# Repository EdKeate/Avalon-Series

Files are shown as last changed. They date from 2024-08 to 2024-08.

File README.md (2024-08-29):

> [!WARNING]
> This Project is a work in progress and not yet finished. Files are uploaded and repository publicised to take onboard feedback, advice and hopefully locate eager collaborators.

> [!WARNING]
> These components are **NOT** compatible with **ANY** Future Motion™ products including, but not limited to: Onewheel, Onewheel+, Onewheel+ XR, Onewheel Pint, Onewheel Pint X, Onewheel GT, Onewheel GT S-series, Onewheel GT S-series "Rally edition".
> 
> Attempting to use **ANY** of the components inside this repository with Future Motion™ products will result in serious injury or death. Do not attempt.

<p align="Center">
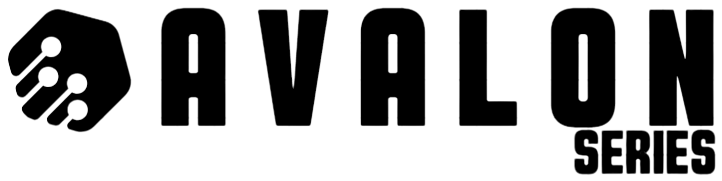
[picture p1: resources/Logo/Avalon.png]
Avalon Logo
  
</p>

---

> **Avalon:** "The isle of the dead, an island paradise where King Arthur and other heroes are taken after death"

The Avalon Project is an open-source Self-Balancing Electric-Skateboard project focused on customizability, power, and networking. All [PCB](https://resources.altium.com/p/what-is-a-pcb), [CAD](https://www.techtarget.com/whatis/definition/CAD-computer-aided-design), Code and project files can be find inside this repository.

> Distributed under the [Apache 2.0 License](https://www.apache.org/licenses/LICENSE-2.0). Read [LICENSE.md](LICENSE.md)

---

- [Odyssey](Odyssey) Flagship 134.4V 1KWh+ Performance System **(ETA: End of Q3 2024)**
- [Apollo:](Apollo) Capable 138.8V 500Wh+ Pocket Rocket **(ETA: End of Q1 2025)**
- [Fenrir:](Fenrir) Powerful 100.8V 400Wh+ Lightweight Commuter **(ETA: Start of Q4 2025)**

>See also: [InfoBar](infobar), E-ink external display for the Avalon Series

---

[](https://github.com/EdKeate/Avalon-Series?tab=readme-ov-file#odyssey)

> On the [Odyssey](https://www.britannica.com/topic/Odyssey-epic-by-Homer), Odysseus faces numerous trials, including monsters and gods, on his decade-long journey home from the Trojan War to Ithaca.

The **Odyssey** is the Flagship board in the **Avalon Series** of self-balancing boards. Boasting a voltage range of 100.8V to 134.4V, 1KWh+ of capacity, 1k+ Lumen lighting (yes actually), Movement wake detection and Fingerprint Sensing (no, seriously). No compromises were taken during the design process. 

> [!IMPORTANT]
> Please read [Odyssey Board Disclaimer](#odyssey-board-disclaimer)

### Features
- Voltage(V): 134.4V to 100.8V
- Range(Km): 50-90 (134.4V), 40-60 (100.8V)
- Speed: [Yes](https://www.youtube.com/watch?v=zXf44tSWhBQ) (Over 2000W+ compared to video)
- 10 x [70-100 Lumen White LEDs](https://www.lcsc.com/datasheet/lcsc_datasheet_2309141627_JNJ-OPTOELECTRONICS-JNJ-LTJH0111W60-26mil-8000-9000K_C7500127.pdf) (PWM Configurable)
- 22 x [SK68812RGBW](https://cdn-shop.adafruit.com/product-files/2757/p2757_SK6812RGBW_REV01.pdf) Addressable LEDs
- [Fingerprint Sensor](https://cdn.shopify.com/s/files/1/0176/3274/files/104474-datasheet.pdf?v=1650622001) with user profiles and logging
- [ESPHome](https://esphome.io/) integration

### Powertrain 
- Controller: [JetFleet F6](https://www.jetfleet.store/product/15108255/controller-jetfleet-f6), [TRONIC X12](https://tronicsystems.com/products/x12-bareboard-no-enclosure), [ENNOID-ESC MK8](https://www.ennoid.me/esc/150v-esc)
- BMS: [ENNOID-BMS Master-XLITE](https://www.ennoid.me/bms/master-xlite), [ENNOID-BMS XLITE-V4](https://www.ennoid.me/bms/xlite-v4), [Flipsky 4S-30S 20A BMS](https://flipsky.net/collections/bms/products/flipsky-4s-30s-20a-bms-protection-board-hardware-ternary-polymer-lithium-battery-only-charge-bms-board-for-onewheel-ebik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)
- Cells: [Molicel P42A](https://www.molicel.com/wp-content/uploads/INR21700P42A-V4-80092.pdf), [Molicel P45B](https://www.molicel.com/wp-content/uploads/INR21700P45B_1.2_Product-Data-Sheet-of-INR-21700-P45B-80109.pdf), [Samsung 50S](https://www.dnkpower.com/wp-content/uploads/2022/07/SAMSUNG-INR21700-50S-Cell-Specification.pdf), [EVE 40P](https://www.rcscomponents.kiev.ua/datasheets/INR21700_40P.pdf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), [Samsung 40T](https://www.dnkpower.com/wp-content/uploads/2019/02/SAMSUNG-INR21700-40T-Datasheet.pdf), [TenPower 40TG](https://www.tenpowercell.com/wp-content/uploads/2022/12/TP-INR21700-40TG-Product-Datasheet-v1.4.1.pdf), [Sony VT6A](https://www.imrbatteries.com/content/murata_us21700vtc6a.pdf)
> If you are unsure what Cell, Controller or BMS to use for this board, consider consulting an experienced VESC builder for assembly assistance. Please refer them to this repository.

### Image
<p align="Center">
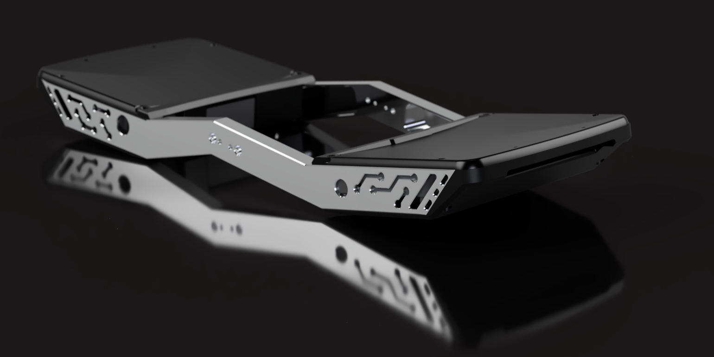
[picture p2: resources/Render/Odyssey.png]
Odyssey Frame
  
</p>

## Odyssey Parts

- [Odyssey Control Board](#odyssey-control-board)
- [Odyssey Lightsym Bars](#odyssey-lightsym-bar)
- [Odyssey Controller Box](#odyssey-controller-box)
- [Odyssey Battery Box](#odyssey-battery-box)
- [Odyssey Rails](#odyssey-rails)
- [Odyssey Footpads](#odyssey-footpads)
- [Odyssey Bumpers](#odyssey-bumpers)
- [Odyssey Fender](#odyssey-fender)
- [Odyssey Axle Blocks](#odyssey-axle-blocks)
- [Avalon Series Tools & Hardware](#avalon-series-tools--hardware)

## Odyssey Control Board

[EasyEDA Files](Odyssey/Control%20Board/PCBs/EasyEDA)

[ESP32 Code + Flashing](Odyssey/Control%20Board/Code)

The **Odyssey Control Board** is designed inside [EasyEDA](EasyEDA.com) and is intended to be assembled using [JLCPCB Economic Assembly](https://jlcpcb.com/capabilities/pcb-assembly-capabilities). 

The Control Board communicates with/powers:
- The [R503-M22 Fingerprint Sensor](https://cdn.shopify.com/s/files/1/0176/3274/files/104474-datasheet.pdf?v=1650622001) 
- 2 x [Odyssey Lightsym Bars](#odyssey-lightsym-bar)
- ESP Home integration using an [Espressif Systems ESP32-WROOM-32E-N8](https://www.lcsc.com/datasheet/lcsc_datasheet_2403071012_Espressif-Systems-ESP32-WROOM-32E-N8_C701342.pdf) as the [MCU](https://en.wikipedia.org/wiki/Microcontroller)
- VESC Power ([SSR Relay](https://www.lcsc.com/datasheet/lcsc_datasheet_1808101047_TOSHIBA-TLP172GM-TPL-E-O_C261926.pdf) control)

### Always on efficiency
The Control board is an **Always-On** Deep-Sleep system, this may cause concerns over [parasitic drain](https://www.uti.edu/blog/automotive/parasitic-battery-drain) for some users, however, the ultra-efficient design and massive battery pack allows for over ~25 years battery life while active. Below shows an example of how to calculate this for yourself:

1. [ESP32](https://www.espressif.com/sites/default/files/documentation/esp32_datasheet_en.pdf) Power consumption (Active)

$$
P_{active} = V_{out} \times I_{active}
$$

$$
P_{active} = 3.3V \times 240mA = 792mW
$$

$$
P_{in} = \frac{P_{active}}{\text{LDO Efficiency}}
$$

$$
P_{in} = \frac{792mW}{0.66} = 1.2W
$$

2. [ESP32](https://www.espressif.com/sites/default/files/documentation/esp32_datasheet_en.pdf) Power consumption (Deep-Sleep)

$$
P_{deep-sleep} = V_{out} \times I_{deep-sleep}
$$

$$
P_{deep-sleep} = 3.3V \times 10\mu A = 33\mu W
$$

$$
P_{in-deep-sleep} = \frac{P_{deep-sleep}}{0.66} = 50\mu W
$$

3. Account for [buck converter efficiency](https://www.meanwellusa.com/upload/pdf/RDDW60/RSDW60,RDDW60-spec.pdf) (Active)

$$
P_{bat} = \frac{P_{in}}{\text{Buck Efficiency}} 
$$

$$
P_{bat} = \frac{1.2W}{0.89} = 1.35W 
$$

**High Voltage**

$$
I_{in} = \frac{P_{bat}}{V_{battery}} = \frac{1.35W}{126V} \approx 10.7mA
$$

**Low Voltage**

$$
I_{in} = \frac{P_{bat}}{V_{battery}} = \frac{1.35W}{90V} \approx 15mA
$$

4. Average Current Calculation (Active)

$$
I_{active} = \frac{10.7mA + 15mA}{2} \approx 12.85mA
$$

5. Account for [buck converter efficiency](https://www.meanwellusa.com/upload/pdf/RDDW60/RSDW60,RDDW60-spec.pdf) (Deep-sleep)

$$
P_{bat-deep-sleep} = \frac{50\mu W}{0.89} = 56\mu W 
$$

**High Voltage**

$$
I_{deep-sleep} = \frac{P_{bat-deep-sleep}}{126V} \approx 0.44\mu A
$$

**Low Voltage**

$$
I_{deep-sleep} = \frac{P_{bat-deep-sleep}}{90V} \approx 0.62\mu A
$$

6. Average Current Calculation (Deep-Sleep)

$$
I_{deep-sleep-avg} = \frac{0.44\mu A + 0.62\mu A}{2} \approx 0.53\mu A
$$

7. Average Current consumption (Combined 5min intervals)

$$
I_{avg} = 12.85mA \times \frac{1}{300} + 0.53\mu A \times \frac{299}{300}
$$

$$
I_{avg} \approx 0.0428mA + 0.53\mu A \approx 0.043mA
$$

8. Battery Capacity Input

$$
\text{Battery Life} = \frac{10,000 mAh}{43\mu A} \approx 232,558 hours = 9689 days = 26.5 years
$$

> [!NOTE]
> Odyssey Control board will enter recovery mode when low voltage (2.7*Series Count). Deep-SLeep interval is upped to a locked 1 hour interval when below threshold. 

>You will also need to purchase parts from [Digikey](https://www.digikey.co.uk/en/mylists/list/NP048JOWBK). See [Electronics Purchasing Guide](#Electronics-Purchasing-Guide) for more information.

> [!CAUTION]
> The Odyssey Control Board is uses the high voltage battery DC input. Ensure proper safety measures are used to prevent damage to ~~battery~~ everything ~~within 5 mile radius~~.
#### Schematic

<p align="Left">
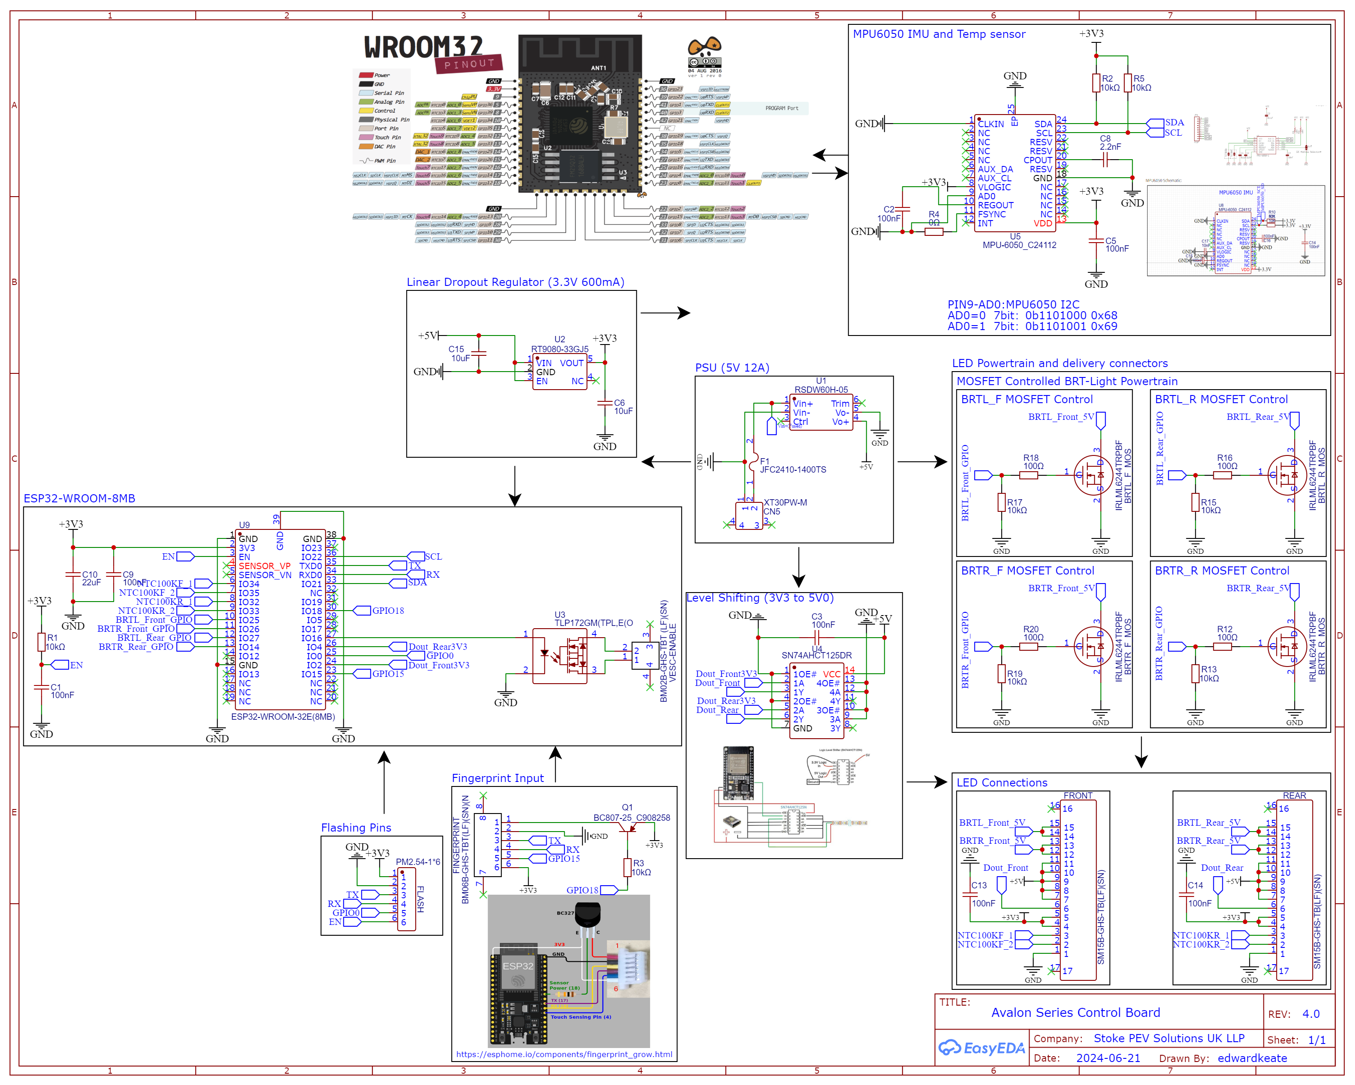
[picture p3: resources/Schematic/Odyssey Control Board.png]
Odyssey Control Board Schematic
  
</p>

#### PCB

**Top**

<p align="Left">
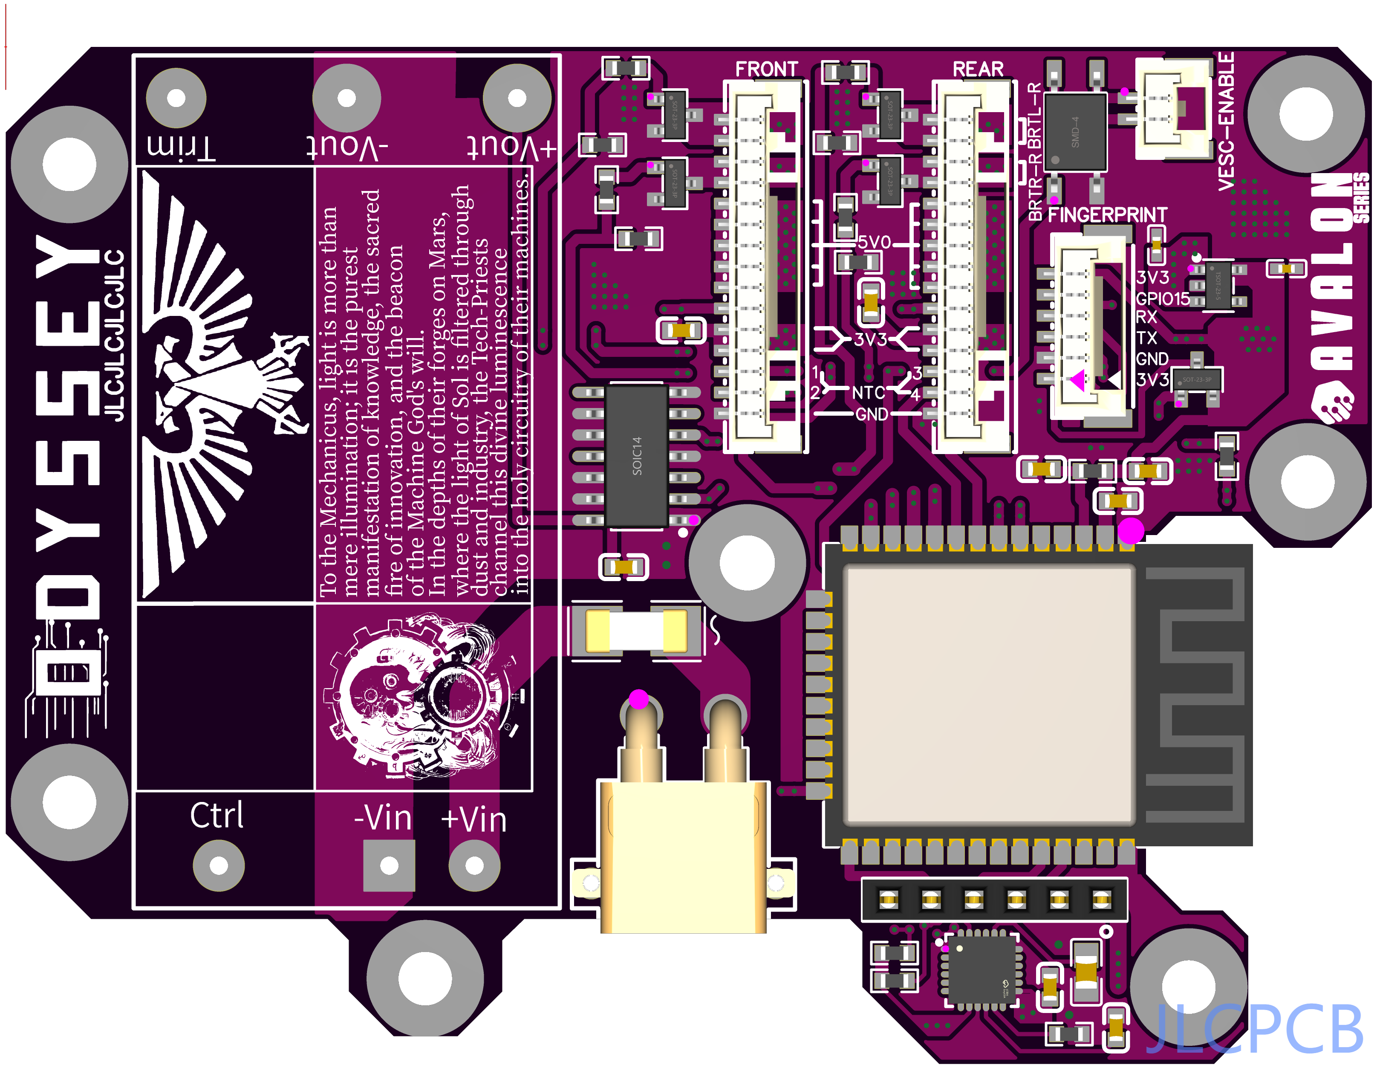
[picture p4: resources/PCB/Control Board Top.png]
Odyssey Control Board PCB (Top)
  
</p>

**Bottom**

<p align="Left">
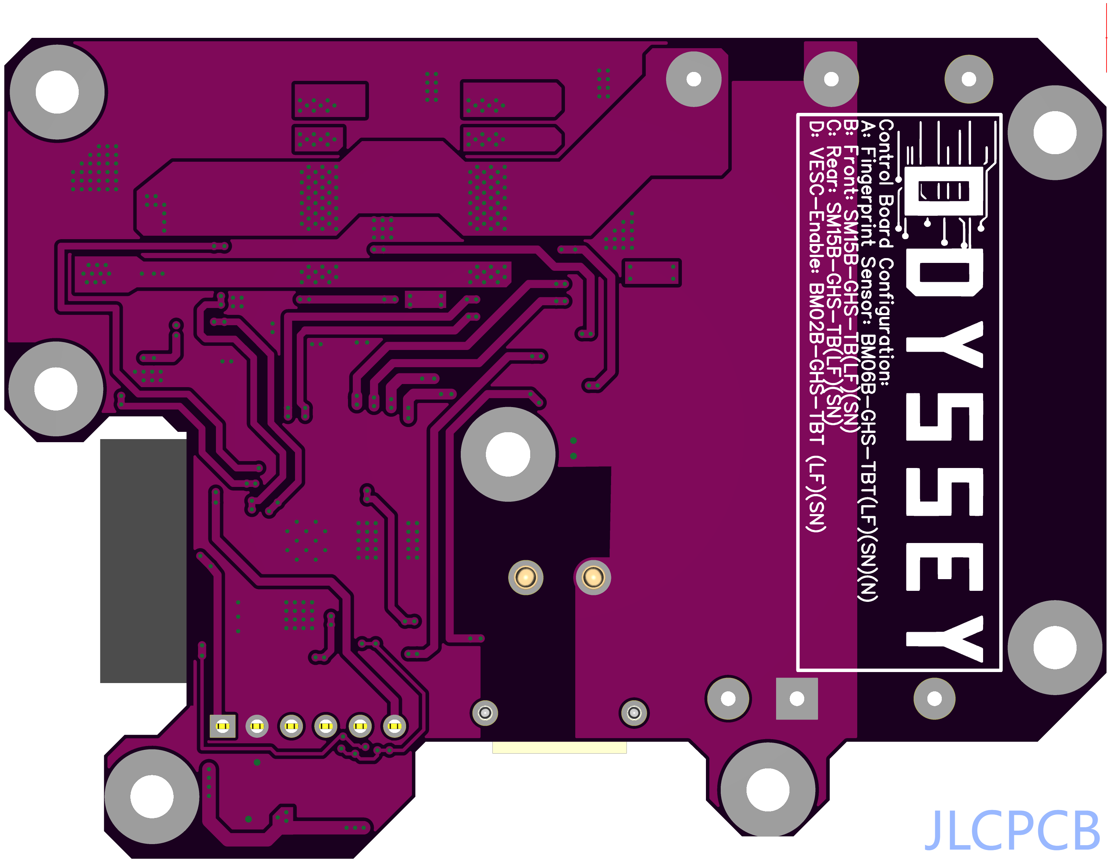
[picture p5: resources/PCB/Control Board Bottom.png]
Odyssey Control Board PCB (Bottom)
  
</p>

> [!TIP]
> Control Boards are designed for expandability. A powerful and efficient 5V rail is integrated into the Schematics, but not the PCB or BOM. See [files](Odyssey/Control%20Board/PCBs/EasyEDA) for more information.

## Odyssey LightSym Bar
[EasyEDA Files](Odyssey/LightSym%20Bar/PCBs/EasyEDA)

The **Odyssey LightSym Bar** is designed inside [EasyEDA](EasyEDA.com) and is intended to be assembled using [JLCPCB Economic Assembly](https://jlcpcb.com/capabilities/pcb-assembly-capabilities). 

The LightSym Bar has 15 inputs:
- 5 x 5V
- 2 x 3V3
- 2 x NTC100K
- 2 x BRTL
- 2 x BRTR
- 1 x Din
- 1 x GND

The labels on these inputs correlates with the labels on the [Odyssey Control Board](#odyssey-control-board).

> You will also need to purchase parts from [Digikey](https://www.digikey.co.uk/en/mylists/list/NP048JOWBK). See [Electronics Purchasing Guide](#electronics-purchasing-guide) for more information.
#### Schematic

<p align="Left">
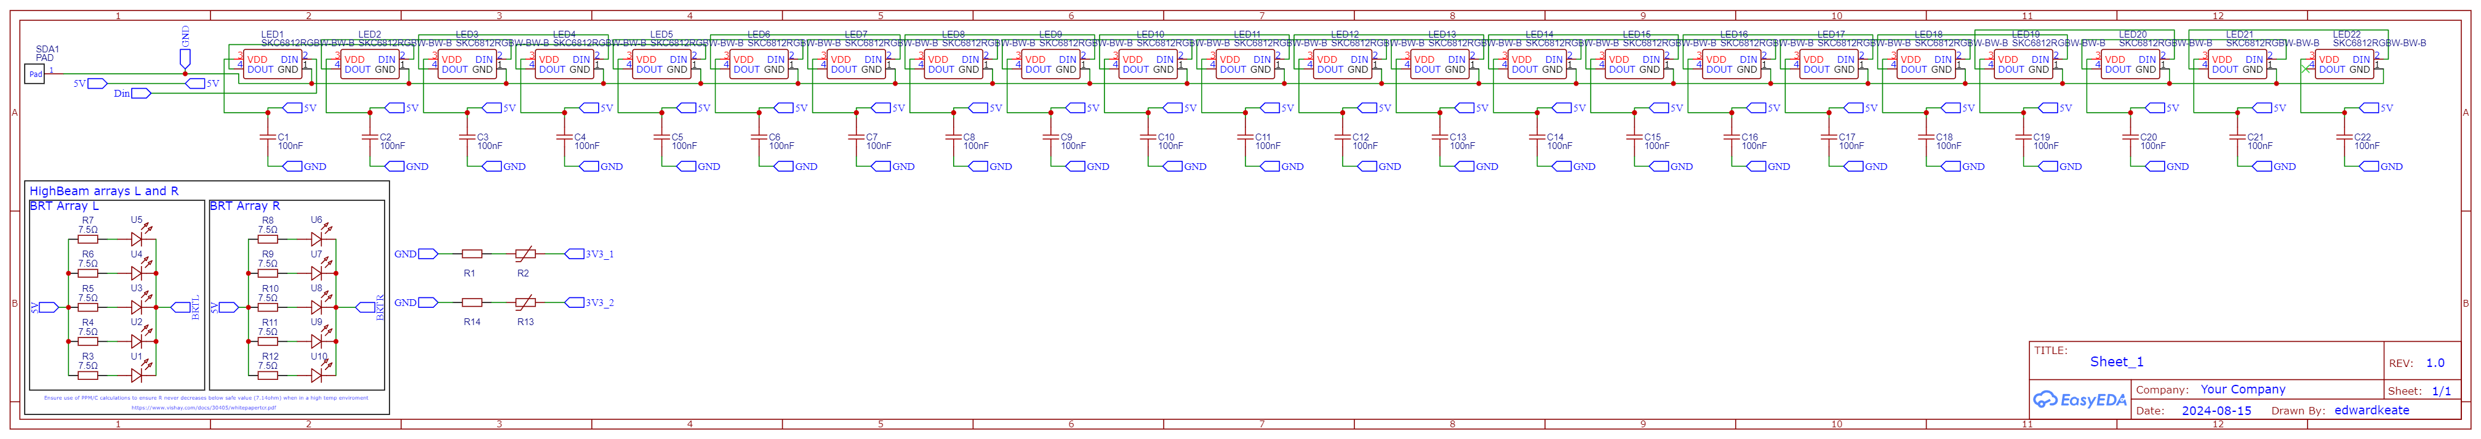
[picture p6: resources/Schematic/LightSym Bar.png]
OdysseyLightSym Bar Schematic
  
</p>

#### PCB

**Top**

<p align="Left">
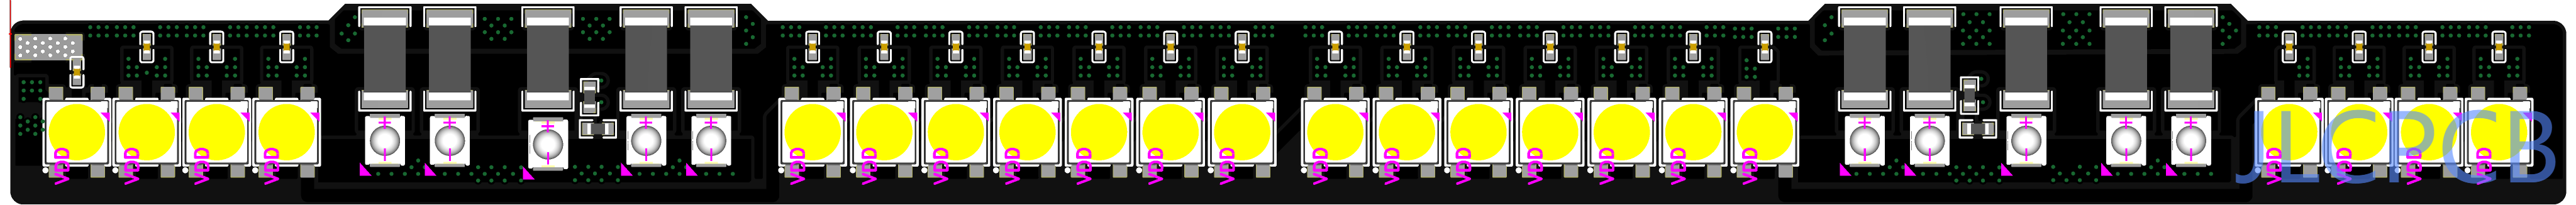
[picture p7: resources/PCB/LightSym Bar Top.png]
Odyssey LightSym Bar PCB Top
  
</p>

**Bottom**

<p align="Left">
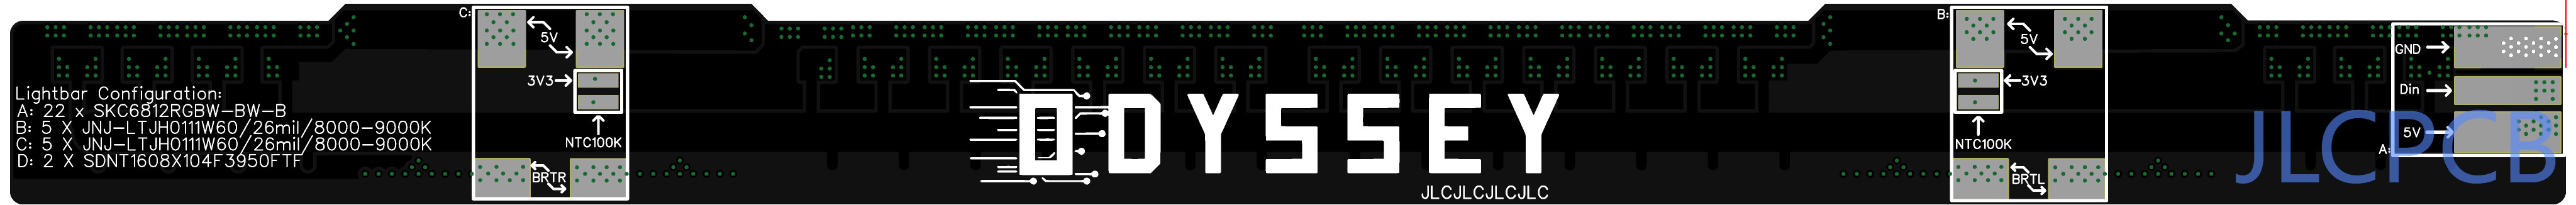
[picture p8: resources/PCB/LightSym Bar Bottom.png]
Odyssey LightSym Bar PCB Bottom
  
</p>

## Odyssey Controller Box
[CAD Files](Odyssey/Controller%20Casing)

The **Odyssey Controller Box** is a split pack enclosure designed for 6S2P 21700. For Controller & Cell options, please see the [Powertrain](#powertrain) section. 
### Features:
- **Dual** [TPU](https://formlabs.com/uk/blog/complete-guide-tpu-3d-printing/) O-ring
- [R503-M22 Fingerprint Sensor](https://cdn.shopify.com/s/files/1/0176/3274/files/104474-datasheet.pdf?v=1650622001) 
- [Superflux Connector](https://www.fungineers.us/products/superflux-female-connector)
- Dual Compartment Design
- M20 Gland Hole
- Steel reinforcement bolt system

> [!TIP]
>See the [Odyssey 3D Printing Guidelines](#odyssey-3d-printing-guidelines) for information on how to manufacture your Controller Box.
#### Image

<p align="Left">
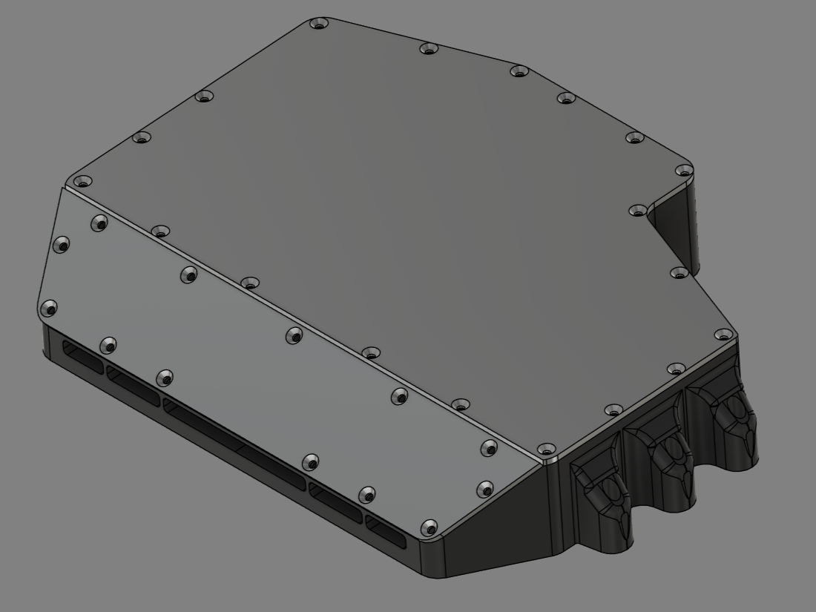
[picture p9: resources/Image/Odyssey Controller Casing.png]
Odyssey Controller Casing Image
  
</p>

#### Render

<p align="Left">
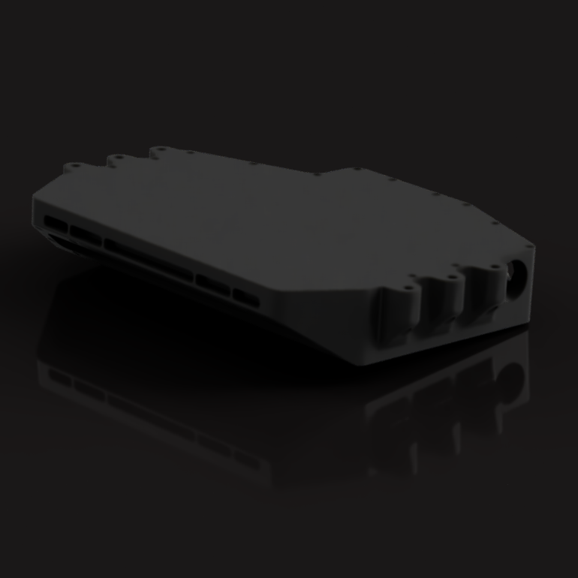
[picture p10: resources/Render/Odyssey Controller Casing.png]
Odyssey Controller Casing Render
  
</p>

## Odyssey Battery Box
[CAD Files](Odyssey/Battery%20Casing)

The **Odyssey Battery Box** has capacity for 24S2P 21700. For cell and BMS options, please see the [Powertrain](#powertrain) section. 
### Features:
- **Dual** [TPU](https://formlabs.com/uk/blog/complete-guide-tpu-3d-printing/) O-ring
- [GX16](https://www.sunrom.com/download/663.pdf) Charge port
- M20 Gland Hole
- Steel reinforcement bolt system

> [!TIP]
>See the [Odyssey 3D Printing Guidelines](#odyssey-3d-printing-guidelines) for information on how to manufacture your Battery Casing.
#### Image

<p align="Left">
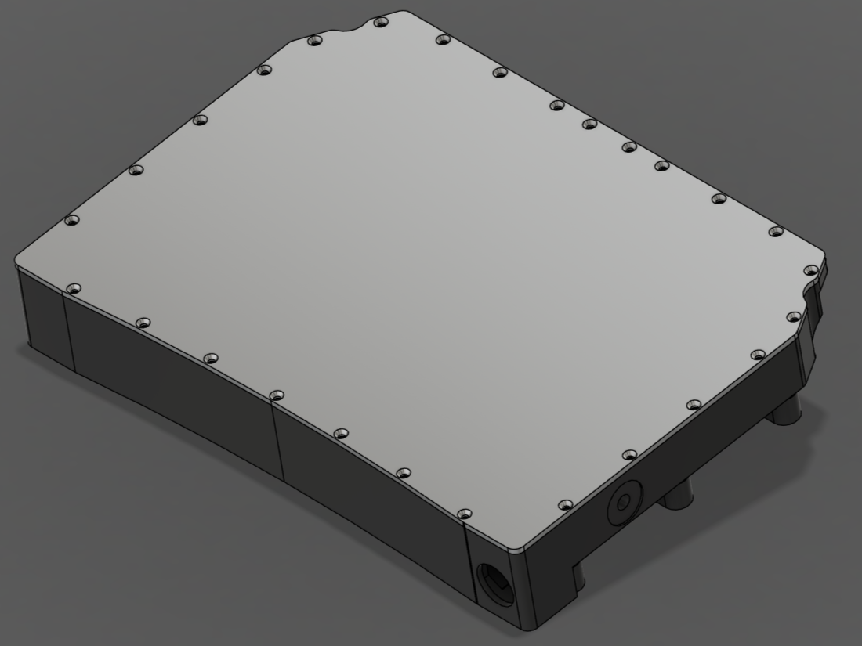
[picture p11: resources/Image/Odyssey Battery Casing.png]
Odyssey Battery Casing Image
  
</p>

#### Render

<p align="Left">
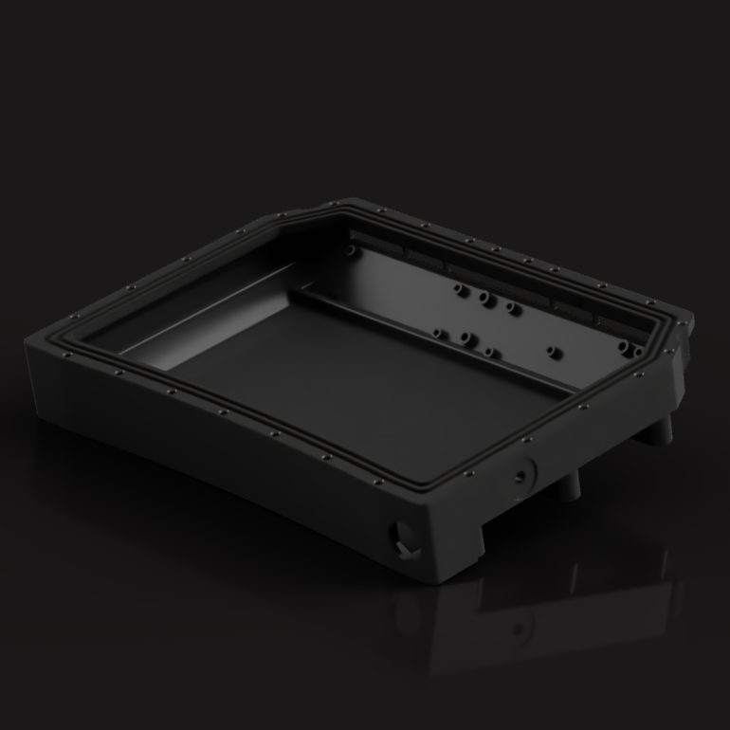
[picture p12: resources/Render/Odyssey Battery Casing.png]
Odyssey Battery Casing Render
  
</p>

## Odyssey Series Rails
[CAD Files](Odyssey/Rails)

The **Odyssey Series** has several unique rail designs. Find yours here:
- [Odyssey Rails](#Odyssey-rails)
- [Odyssey Rails (Skeletonised)](#Odyssey-rails)
### Odyssey Rails (Skeletonised)
The Flagship rails. Designed to be **lighter-weight** and strong using a completely unique skeletisation design. 
**Statistics:**
- 12" wheel-well (BTG)
- Unique "Trace" skeletisation
- 5°lowered, 3° lifted
- 4° tail lift
#### Image

**Left Rail**

<p align="Left">
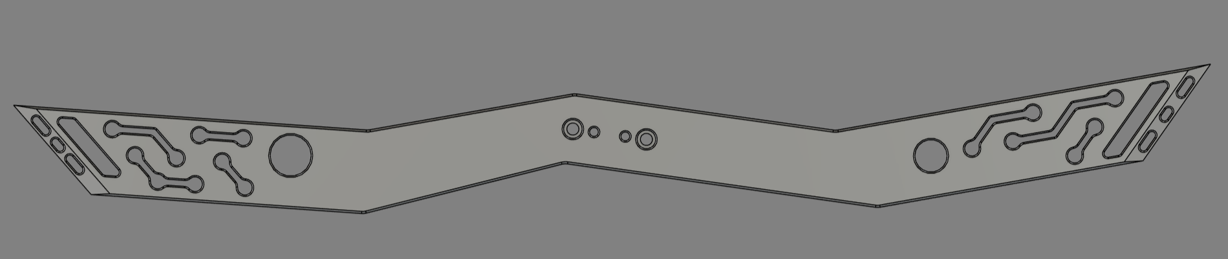
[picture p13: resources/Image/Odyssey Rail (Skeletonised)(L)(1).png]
Odyssey Rail (Skeletonised)(L)(1)
  
</p>

<p align="Left">
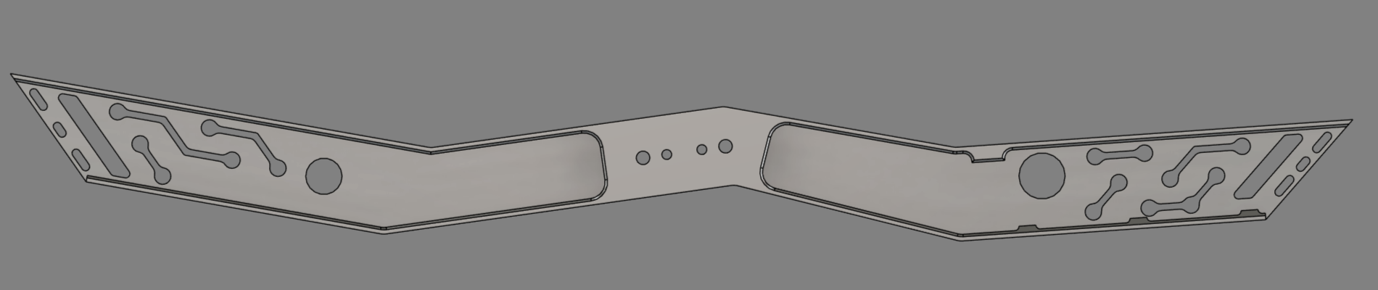
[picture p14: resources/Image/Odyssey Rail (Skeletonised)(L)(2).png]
Odyssey Rail (Skeletonised)(L)(2)
  
</p>

**Right Rail**

<p align="Left">
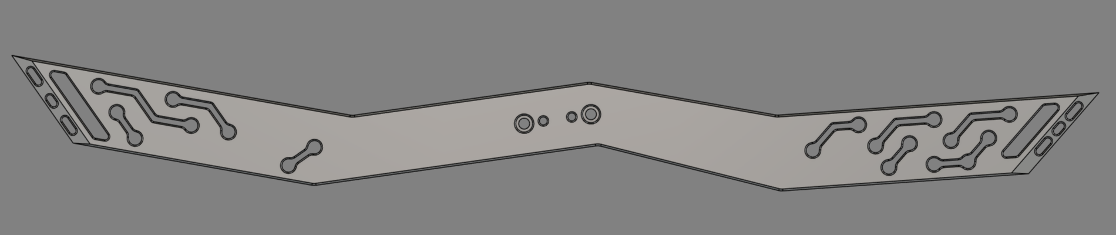
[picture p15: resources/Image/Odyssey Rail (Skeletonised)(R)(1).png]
Odyssey Rail (Skeletonised)(R)(1)
  
</p>

<p align="Left">
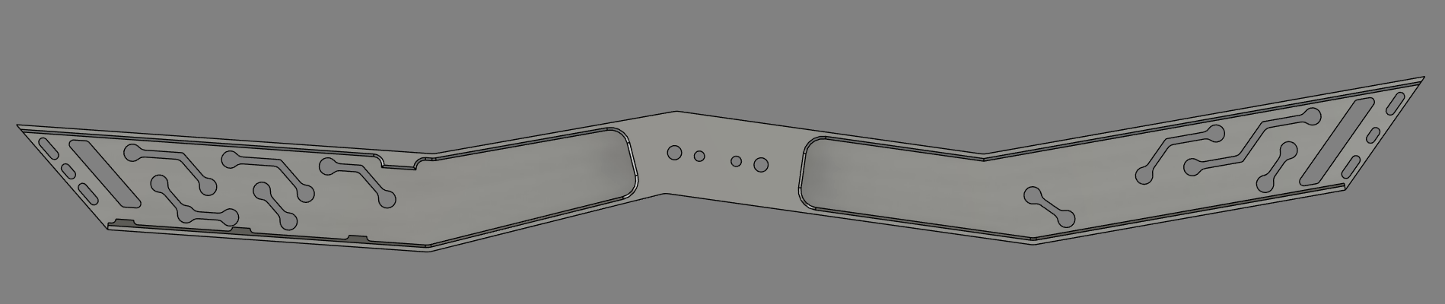
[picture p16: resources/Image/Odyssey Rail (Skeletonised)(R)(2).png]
Odyssey Rail (Skeletonised)(R)(2)
  
</p>

### Odyssey Rails
Cheaper Flagship rails. Designed to be **light-weight** and strong at a lower cost. 
**Statistics:**
- 12" wheel-well (BTG)
- 5°lowered, 3° lifted
- 4° tail lift

#### Image

<p align="Left">
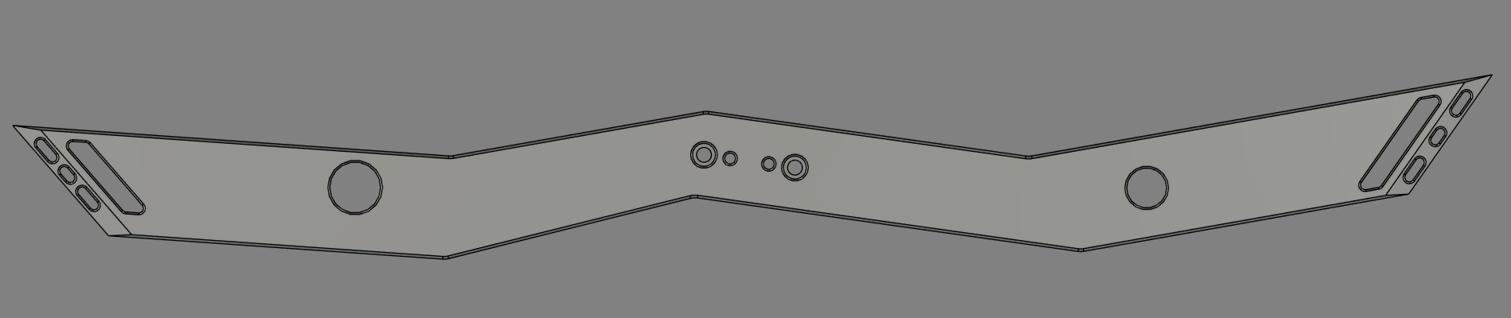
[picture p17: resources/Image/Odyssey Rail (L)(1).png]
Odyssey Rail (L)(1)
  
</p>

<p align="Left">
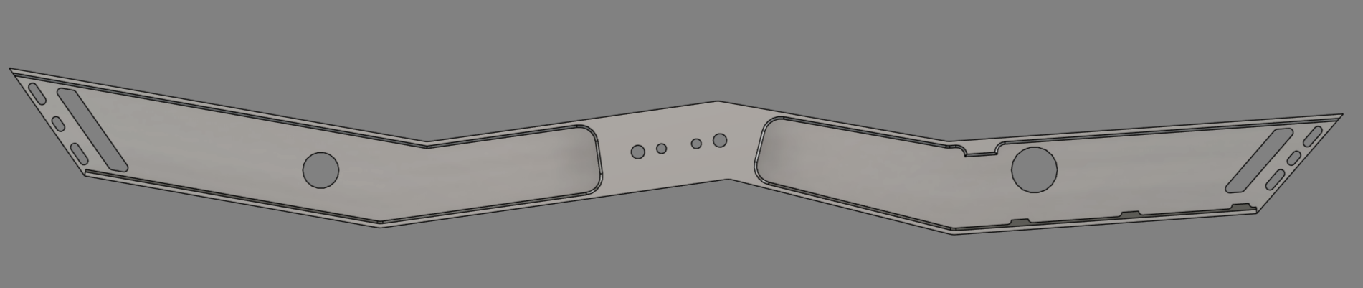
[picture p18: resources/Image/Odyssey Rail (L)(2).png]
Odyssey Rail (L)(2)
  
</p>

**Right Rail**

<p align="Left">
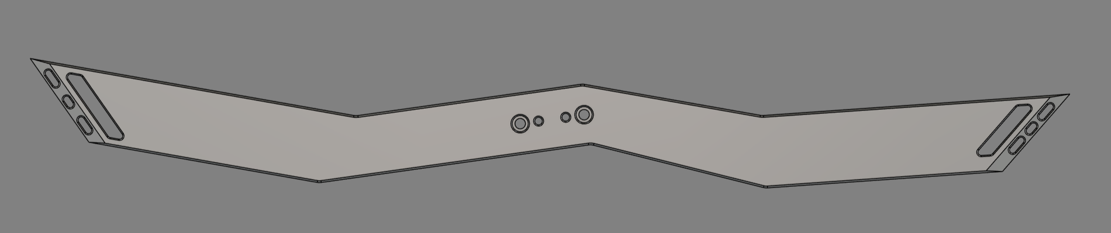
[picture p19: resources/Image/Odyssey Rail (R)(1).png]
Odyssey Rail (R)(1)
  
</p>

<p align="Left">
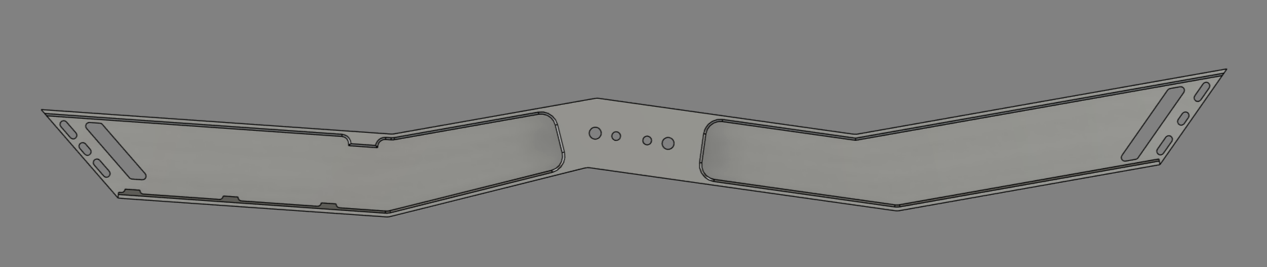
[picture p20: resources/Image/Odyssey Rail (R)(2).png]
Odyssey Rail (R)(2)
  
</p>

> [!TIP]
>See the [Avalon Machining Guidelines](#avalon-machining-guidelines) for information on how to manufacture your Rails.

## Odyssey Footpads

[CAD Files](Odyssey/Footpads)

The **Odyssey Footpads** take inspiration from [Stanley Shaw's](https://vow.systems/) [Mushies](https://vow.systems/products/gt-mushies). Go check out his designs!

**Features:**
- Supports hard([PLA](https://help.prusa3d.com/article/pla_2062), [ASA](https://help.prusa3d.com/article/asa_1809)) or Soft ([TPU](https://ninjatek.com/shop/ninjaflex/)) [FDM](https://www.hubs.com/knowledge-base/what-is-fdm-3d-printing/) printing for hard or soft footpads
- Mirrored pads (Same design front and rear)
- Light Concave
- Super thin for locked-in feel

#### Image

<p align="Left">
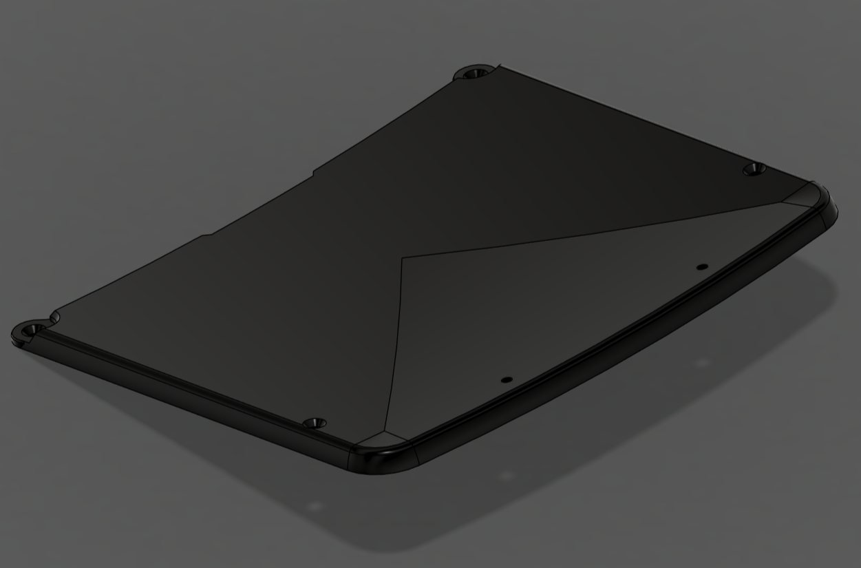
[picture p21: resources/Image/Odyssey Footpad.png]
Odyssey Footpad Image
  
</p>

#### Render

<p align="Left">
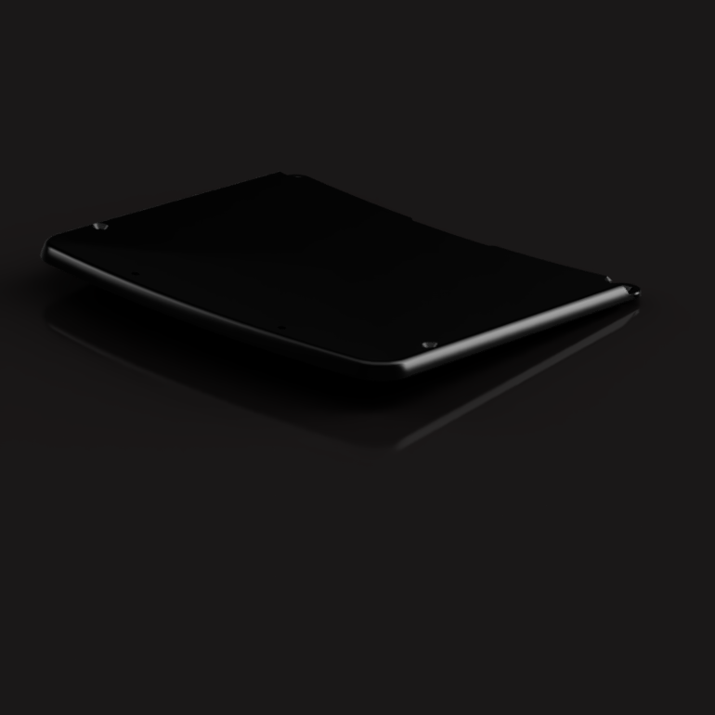
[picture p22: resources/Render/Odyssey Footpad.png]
Odyssey Footpad Render
  
</p>

> [!TIP]
>See the [Odyssey 3D Printing Guidelines](#odyssey-3d-printing-guidelines) for information on how to manufacture your Footpads.

## Odyssey Bumpers
[CAD Files](Odyssey/Bumpers)

The **Odyssey Bumpers** are ultra-durable symmetrical bumpers designed for CNC [UHMWPE](https://www.hubs.com/cnc-machining/plastic/hdpe/uhmwpe/) or [FDM](https://www.hubs.com/knowledge-base/what-is-fdm-3d-printing/) manufacturing. 

**Features:**
- Supports [FDM](https://www.hubs.com/knowledge-base/what-is-fdm-3d-printing/) printing or [UHMWPE](https://www.hubs.com/cnc-machining/plastic/hdpe/uhmwpe/) manufacturing.
- Symmetrical front and back bumpers
- Ultra-thin, yet durable
- Multiple Mounting configurations
#### Image

<p align="Left">
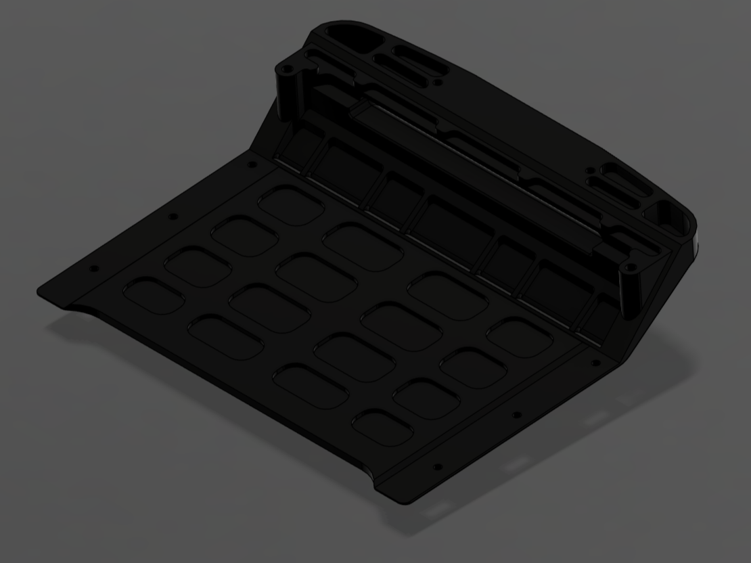
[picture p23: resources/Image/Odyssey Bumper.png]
Odyssey Bumper Image
  
</p>

#### Render

<p align="Left">
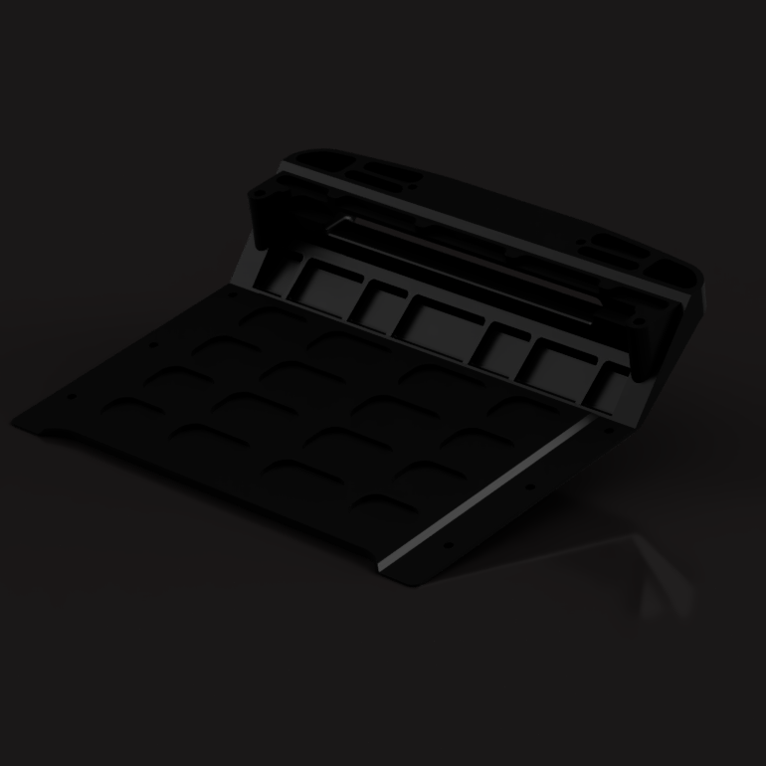
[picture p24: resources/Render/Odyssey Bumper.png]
Odyssey Bumper Render
  
</p>

> [!TIP]
>See both the [Odyssey 3D Printing Guidelines](#odyssey-3d-printing-guidelines) and [Avalon Machining Guidelines](#avalon-machining-guidelines) to determine your manufacturing method.

## Odyssey Fender
[CAD Files](Odyssey/Fender)

The **Odyssey Fenders** are optional add-ons for your Odyssey board that further protect the [Odyssey Battery Box](#odyssey-battery-box) and [Odyssey Controller Box](#odyssey-controller-box) from corrosion.

**Features:**
- Super small [FDM](https://www.hubs.com/knowledge-base/what-is-fdm-3d-printing/) print
- Integrated shell covers for O-rings and Connectors to further protect against water ingress.

#### Image

<p align="Left">
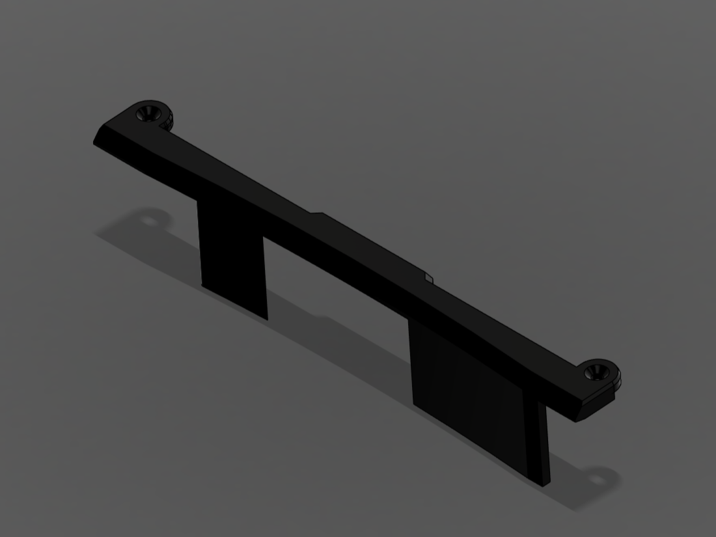
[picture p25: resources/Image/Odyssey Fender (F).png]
Odyssey Controller Fender(F)
  
</p>

<p align="Left">
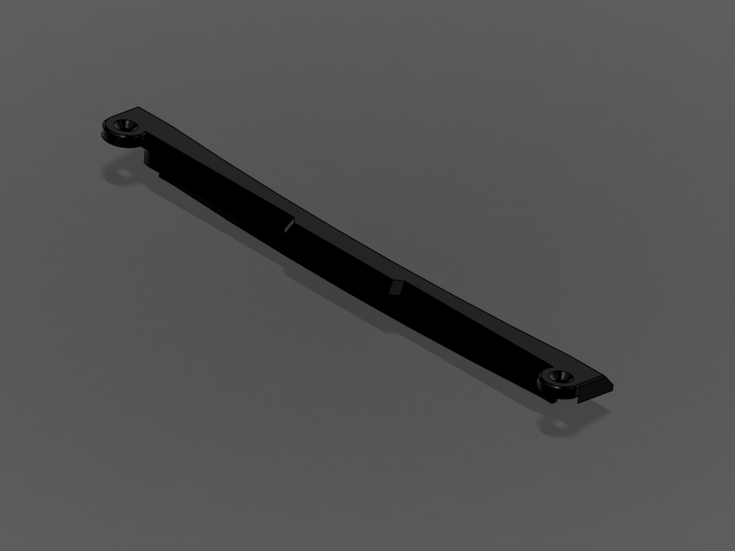
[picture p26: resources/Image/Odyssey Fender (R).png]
Odyssey Controller Fender(R)
  
</p>

> [!TIP]
>See the [Odyssey 3D Printing Guidelines](#odyssey-3d-printing-guidelines) for information on how to manufacture your Fenders.

## Odyssey Axle Blocks
[CAD Files](Odyssey/Axle%20Blocks)
TBD

# Odyssey 3D Printing Guidelines

> [!IMPORTANT]
> If you aren't used to 3D printing or don't know where to start, I would recommend consulting an expert. Due to the dangerous nature of all self-balancing devices, 3D prints need to be strong, accurate and reliable.

## Solid Prints
Below, you can find the material recommendations and mechanical requirements for **SOLID** 3D prints for the **Odyssey Series** of Board. 

### Minimum Specification
These are the absolute minimum requirements for 3D printing the **Odyssey series** solid components:
- Print Volume: 350mm x 350mm x 150mm 
- Material: [ABS](https://www.prusa3d.com/category/asa-abs/), [ASA](https://www.prusa3d.com/category/prusament-asa/), [PETG](https://www.prusa3d.com/category/prusament-petg/)
- Wall Thickness: 2-3x nozzle diameter
- Infill: >15%
> [How to make 3D prints waterproof](https://all3dp.com/2/waterproof-3d-print-pla/)
### Recommended Specification
- Material: [PC-CF](https://www.prusa3d.com/product/prusament-pc-blend-jet-black-970g/), [PA (Nylon)](https://www.prusa3d.com/category/prusament-pa-nylon/)
- [Support Material](https://dddrop.com/3d-printing-with-support-material/) (Ideally [Water Soluble](https://www.stratasys.com/en/materials/materials-catalog/fdm-materials/fdm-support-materials/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,submerged%20in%20the%20dissolution%20tank.))
- Infill: >20% ([Honey Pattern](https://all3dp.com/2/get-cura-honeycomb-infill/))

## Flexible Prints

Below, you can find the material recommendations and mechanical requirements for **FLEXIBLE** 3D prints for the **Odyssey Series** of Board.
### Minimum Specification
These are the absolute minimum requirements for 3D printing the **Odyssey series** flexible components
- Print Volume: 350mm x 350mm x 100mm 
- Material: [TPU](https://ninjatek.com/shop/ninjaflex/)
- Infill: 100%

> You are expected to find your own 3D printer that meets these requirements. If this is outside of your budget, consider a 3D printing service.

---

### Odyssey Board Disclaimer

>The Odyssey is, by far, the heaviest and largest board ever made. This is a personal proof of concept/hobby for myself to show the absolute insanity of todays open-source/manufacturing technology and is NOT meant to be a consumer product. If you are passionate, and I mean PASSIONATE about Balance Boards, this is your next project.

>The Avalon Series is based upon [ESPHome](https://esphome.io/) so that others can build upon the simple, yet powerful [YAML language](https://esphome.io/guides/getting_started_command_line.html) it uses. Some of the schematics have in-built but unused experimental modules for modification. For example, the [InfoBar](#infobar) (as of V1.0.0) does not use any 5V electronics, yet the schematic includes a 5V buck converter for the Battery. This is excluded from the [BOM](https://jlcpcb.com/help/article/bill-of-materials-for-pcb-assembly) and PCB, however it would be fairly easy to integrate with little [PMIC](https://en.wikipedia.org/wiki/Power_management_integrated_circuit) experience. I understand that electronics are not for everyone, however I would love to see more people getting into the nitty gritty and picking up electronics as a hobby.

>If you do decide to build this board, you will never need a more powerful, longer range or higher speed board. As an experienced VESC builder and PCB designer, this has every technology that I currently understand implemented and turned up to 11, it's not meant to be simple to build, nor is it intended to be mass produced. The Pathfiner and Questor are much more practical, yet significantly less capable boards, however they are for the everyman, this is not.

>Another important note is the license. I am using the [Apache 2.0 License](http://www.apache.org/licenses/LICENSE-2.0) as it offers protection over liability and warranty (I am not a legal professional). This is not a malicious attempt to shift blame to the builder, but a way to protect myself against legal action. [Self-balancing devices are inherently dangerous](https://www.lawsuit-information-center.com/onewheel-injury-lawsuits-against-future-motion.html) and I am in no way a proffessional, I find it important that I can continue to work on this project for the forseeable future without concerns over venturing into new technologies. 

>I have no plans to profit from these designs, nor do I have any plans to sell boards directly, especially since that would be [illegal](https://patents.google.com/patent/US9101817B2/en). However, I am available to comission to assemble some of the more complicated components.

---

# Apollo

> Swift and tireless, [Apollo](https://www.britannica.com/topic/Apollo-Greek-mythology) races the sun across the sky each day, his boundless energy unmatched, guiding light and life with unyielding endurance.

The **Apollo** is the Lightest board in the **Avalon Series** of self-balancing boards. Boasting a 126.8V to 134.4V, 500Wh+ Capacity and 300+ Lumen lighting, the Apollo is the ideal Pocket Rocket. Contains Avalon exclusive features such as: IMU wake detection, Fingerprint Sensing, ESPHome integration etc.

> [!IMPORTANT]
> Please read [Apollo Board Disclaimer](#apollo-board-disclaimer)

### Features
- Voltage(V): 126.8V to 134.4V
- Range(Km): 30-40 (134.4V), 25-35 (126.8V)
- Speed: [Yes](https://www.youtube.com/watch?v=zXf44tSWhBQ)
- [Fingerprint Sensor](https://cdn.shopify.com/s/files/1/0176/3274/files/104474-datasheet.pdf?v=1650622001) with user profiles and logging
- [ESPHome](https://esphome.io/) integration

> [!NOTE]
> **Files relating to the Apollo are currently in a private reposity. Information about the board will be released closer to release.**

---

# Fenrir

> A monstrous wolf in Norse mythology, [Fenrir](https://www.britannica.com/topic/Fenrir) is destined to bring about Ragnarök, breaking free from his chains to devour Odin.

The **Fenrir** is the Cheapest board in the **Avalon Series** of self-balancing boards. Utilising 92.8V, 400Wh+ Capacity and 300+ Lumen lighting, the Fenrir is an ultra-durable Split-Pack Trick Board. Contains Avalon exclusive features such as: IMU wake detection, Fingerprint Sensing, ESPHome integration etc.

> [!IMPORTANT]
> Please read [Fenrir Board Disclaimer](#fenrir-board-disclaimer)

### Features
- Voltage(V): 92.8V
- Range(Km): 25-40
- Speed: 25mph+
- [Fingerprint Sensor](https://cdn.shopify.com/s/files/1/0176/3274/files/104474-datasheet.pdf?v=1650622001) with user profiles and logging
- [ESPHome](https://esphome.io/) integration

> [!NOTE]
> **Files relating to the Fenrir are currently in a private reposity. Information about the board will be released closer to release.**

---

# InfoBar
The InfoBar is an [ESPHome](https://esphome.io/) based [E-ink display](https://www.waveshare.com/4.2inch-e-paper-module.htm) with [Automatic PSU switching](https://www.lcsc.com/datasheet/lcsc_datasheet_2304140030_Analog-Devices-LTC4412IS6-TRPBF_C521306.pdf), [Single Cell BMS](https://www.lcsc.com/datasheet/lcsc_datasheet_1912111437_TPOWER-TP4056_C382139.pdf) and a single [USB-C](https://www.lcsc.com/datasheet/lcsc_datasheet_1811151656_HOOYA-USB-310F-B-SU_C309365.pdf) for flashing and charging.
### Features
- 6-month battery life
- 4.2 inch 400x600 resolution [E-ink display](https://www.waveshare.com/4.2inch-e-paper-module.htm)
- Pre-ride weather information (requires configuration)
- Board statistics display (Updates every 5 minutes)
- User Log (Requires [R503 Fingerprint Sensor](https://cdn.shopify.com/s/files/1/0176/3274/files/104474-datasheet.pdf?v=1650622001))

> [!CAUTION]
> The InfoBar can only send/receive information to other devices on the ESPHome system. Do not attempt to integrate with your VESC-based speed controller as this will cause memory and pin allocation issues which will inevitably brick your VESC-based speed controller (The [Odyssey Control Board](#Odyssey-Control-Board) is isolated for a reason)

> [!NOTE]
> User log is stored inside Sensor memory. **Your Biometric data will never be shared to or stored by other individuals without your consent**. 

### Schematic

<p align="Left">
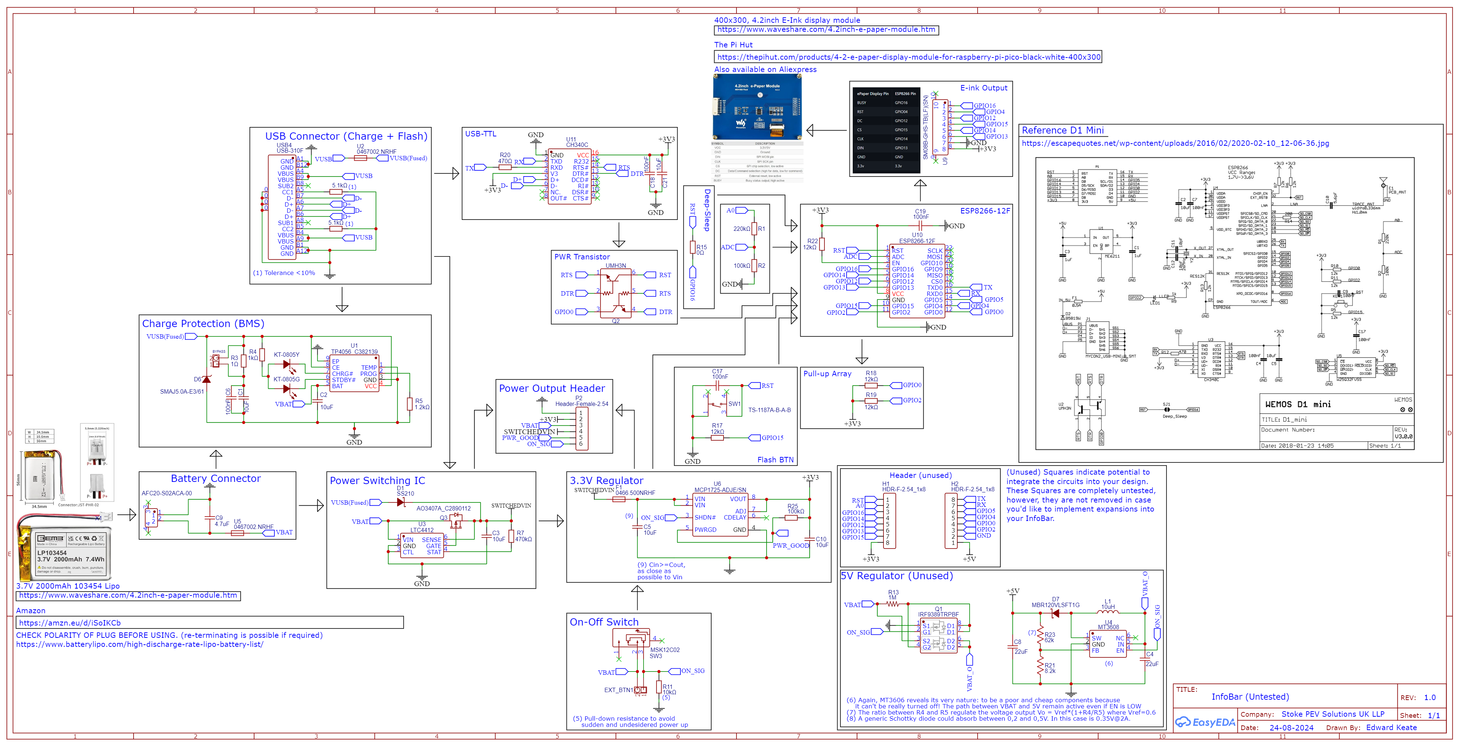
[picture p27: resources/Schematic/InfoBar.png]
InfoBar Schematic
  
</p>

### PCB

TBD

## Assembly
Based on the excellent [HA Sensor ePaper Display](https://github.com/maxmacstn/HA-ePaper-Display) by [Sitinut Waisara](https://github.com/maxmacstn).

# Avalon Machining Guidelines

> [!TIP]
> CNC Manufacturing is expensive, consider taxes, shipping and economy of scale before ordering. If you are a VESC technician considering producing any number of **Avalon Series** Boards, shoot me a message regarding machining.

[hubs.com](https://www.hubs.com)

Below, you can find the guidelines and how-to for manufacturing the .STEP files provided for each CNC component.

### Minimum Specification
These are the absolute minimum requirements for CNC manufacturing **Avalon Series** products:
- Material: [AlMg1SiCu](https://www.hubs.com/cnc-machining/metal/aluminum/aluminum-6061/), [AlSi1MgMn](https://www.hubs.com/cnc-machining/metal/aluminum/aluminum-6082/)
- [Post-Process:](https://www.hubs.com/knowledge-base/surface-finishes-cnc-machinings/) [Bead Blasting](https://www.hubs.com/surface-finishing-services/bead-blasting-services/) / None
### Recommended Specification
- Material: [AlZn5](https://www.hubs.com/cnc-machining/metal/aluminum/aluminum-7075-6/)
- [Post-Process:](https://www.hubs.com/knowledge-base/surface-finishes-cnc-machinings/) [Anodization](https://www.hubs.com/knowledge-base/what-is-anodizing/) [Type II or Type III](https://www.hubs.com/knowledge-base/type-ii-vs-type-iii-anodizing-what-does-your-project-require/)

> [!CAUTION]
> If you **DO NOT** opt for Anodization or another form of post-processing, please ensure you choose a **non-corrosive** metal! 

> [!NOTE]
> You are not expected to know anyone with a CNC Machine. If you happen to, these rails will probably exceed their Machine bed max dimensions. Use a CNC service such as hubs.com for easy turnaround. You will need to tap all M5 threads as they are NOT modelled. See: [Avalon Series Tools & Hardware](#avalon-series-tools--hardware)

# Electronics Purchasing Guide
The **Avalon Series** uses several thousand unique and specialist parts to operate. As these cannot all come from the same source, some assembly is required. 
## Digikey
[Digi-Key](https://www.digikey.com/) is a **global distributor** of electronic components, offering a vast selection of products, tools, and resources for engineers and makers. They are incredibly reliable and a **highly recommended** purchase option.

> [!IMPORTANT]
> You can find a full list of every part I use to make **Avalon Series Boards** via this [Digikey Shared List](https://www.digikey.co.uk/en/mylists/list/NP048JOWBK). You can also source some of the parts from [LCSC](https://www.lcsc.com/) when you purchase the PCBs.

## Adafruit Industries

If you've got the cash, [Adafruit Industries](https://www.adafruit.com/) is a super reliable website supporting great people. I have used plenty of their guides and datasheets to create these boards, so show them some love!

## Aliexpress
If you're working on a budget, Aliexpress offers cheaper but less reliable hardware. Try to avoid purchasing parts from here, but if you do, here's what to watch out for:

 - **Reviews**. 4 Stars+ and 10 reviews is my benchmark, but that may not be easy to find. Also read reviews as bots are rife on the electronics side of Aliexpress. 
 - **Brand**. Sometimes products you can purchase are not identical to the datasheets provided, this may cause communication problems between components. Ideally products are associated with the appropriate brand, this is especially important with powertrain electronics. (Don't buy an Aliexpress VESC)
 - **Connections**. All PCBs have been designed to be compatible with parts from the [Adafruit Industries](https://www.adafruit.com/) website, some products may look similar, but use different connectors. This will require soldering/crimping to fix. 

> [!CAUTION]
> **DO NOT** purchase replacement PCB components from Aliexpress. If you require an SMD fix, purchase from [LCSC](https://www.lcsc.com/) or an equivalent from [Digikey](https://www.digikey.com/)

# Avalon Series Tools & Hardware
The **Avalon Series** requires a lot of tools and miscellaneous parts to assemble. Here is a list of the most important, but not all of the products required to assemble your board.

This section only covers the physical mounting hardware, for electronic parts, see individual components. 

> [!NOTE]
> Tool & Part Links are listed in format: "Name: UK Distributor / US Distributor" where applicable.

> [!IMPORTANT]
> If you're planning on wet riding, ensure you choose [parts resistant to corrosion (A4)](https://www.accu.co.uk/p/114-grades-of-austenitic-stainless-steel#:~:text=and%20UNS%20S30400.-,A4,harsh%20chemical%20and%20outdoor%20environments.).

## Tools
- Pinecil V2 Soldering Iron: [Global](https://pine64.com/product/pinecil-smart-mini-portable-soldering-iron/)
- Wera Kraftform Standard: [UK](https://www.accu.co.uk/bitholding-tools/644674-05051274001) / [US](https://accu-components.com/us/bitholding-tools/644674-05051274001)
- T6 Torx Bit: [UK](https://www.accu.co.uk/drive-bits/636302-HDB-H-T6-HS) / [US](https://accu-components.com/us/drive-bits/636302-HDB-H-T6-HS)
- T10 Torx Bit: [UK](https://www.accu.co.uk/drive-bits/636288-HDB-H-T10-HS) / [US](https://accu-components.com/us/drive-bits/636288-HDB-H-T10-HS)
- T25 Torx Bit: [UK](https://www.accu.co.uk/drive-bits/636292-HDB-H-T25-HS) / [US](https://accu-components.com/us/drive-bits/636292-HDB-H-T25-HS)

> [!TIP]
> If you're working on a budget, a precision screwdriver set can be a good idea.

## Parts
- M2 x 6mm T6 Torx Pan Head Screws: [UK](https://www.accu.co.uk/hexalobular-pan-head-screws/475310-SHP-M2-6-V2-A4) / [US](https://accu-components.com/us/hexalobular-pan-head-screws/475310-SHP-M2-6-V2-A4)
- M2 x 3mm x 3.5mm: [UK](https://amzn.eu/d/bMJwggv) / [US](https://a.co/d/7rllooY)
 - M3 x 8mm T10 Torx Countersunk Screws: [UK](https://www.accu.co.uk/metric-torx-countersunk-screws/474332-SHK-M3-8-V2-A4) / [US](https://accu-components.com/us/metric-torx-countersunk-screws/474680-SHK-M3-8-V2-A4-BL)
 - M3 x 4mm x 5mm Brass Inserts: [UK](https://amzn.eu/d/eGp4Ldr) / [US](https://a.co/d/0UTHYOB)
 - M5 x 16mm T25 Torx Countersunk Screws: [UK](https://www.accu.co.uk/metric-torx-countersunk-screws/474743-SHK-M5-16-V2-A4-BL) / [US](https://accu-components.com/us/metric-torx-countersunk-screws/474744-SHK-M5-16-V2-A4-BL)
 - M5 x 8mm L x 7mm Brass Inserts: [UK](https://amzn.eu/d/6vIgD88) / [US](https://a.co/d/f2SdH9I)

> [!TIP]
> The websites listed are wholesalers due to the large number of duplicate parts. If you haven't used a wholesaler before, try and aim for the lowest price break so you have spares and save money.

# Helping out

Thank you for making it this far through the document, if you're interested in helping out with the Avalon project, but don't know where to start, here's a quick breakdown of all the things that happen behind the scenes before being displayed on this repository. Help is always appreciated!

- PMIC design. Power Management Electronics are a highly detailed and precise part of the layout process. Consultation is important, and considerations of Voltage stabilisation, efficiency and standardisation are vital. I have far-future plans to integrate the designs into the XR, GT, GT-S Series, and Pint Series. Because of this, an incredibly wide array of PMIC devices will be required. If you have experience in PMIC design, let me know!

- ESPHome integration. As someone who has learned YAML entirely for this project, writing code for ESPHome is incredibly time-consuming. Assistance in ensuring security, reliability, and ease-of-use while operating user devices would be greatly appreciated.

- CAD improvements. As an experienced CAD designer, I have no problem creating and designing high strength and reliable designs. However, CNC, FDM and other processes are new to me as of the past few years. I have plenty to learn and would love feedback on the different mistakes I have made on my project.

- Writing guides. As someone who re-learnt HTML and Markdown for this project, the guides take a very long time to write(The main README.md took 10hrs+). if you are patient and want to write assembly tutorials, part guides, re-word specifications, etc, this will greatly help all those who venture down the assembly rabbit hole.

- Design Ideas. No idea is too much. My main focus of the Avalon Series is that it is easy to add to. Browse the ESPHome website and see what would be cool to have on your Onewheel. Here's some things to consider when drafting up your ideas: Can it be waterproofed? How would someone make this themself? How much do other things like this cost?

> [!NOTE]
> My phone number shouldn't be publicly available, however some seem to call or text me out of the blue for technical support. Please use the appropriate method of contacting me through my email, Github or using the Discussion on this page. You're more than welcome to contact me via my number for a chat about something non-Avalon related, however it is unfair on others and myself to hotline directly to me.
> Thanks for understanding :)

> [!TIP]
> The Avalon Project is constantly updating, if you are venturing down the path of building one of these boards, please make sure you check back here frequently for any important notices, issues, or just for some fancy new features.

Shred on! 

Ed

# License
Copyright 2024 Edward Keate
   
Licensed under the Apache License, Version 2.0 (the "License");
you may not use this file except in compliance with the License.
You may obtain a copy of the License at

 > http://www.apache.org/licenses/LICENSE-2.0

Unless required by applicable law or agreed to in writing, software
distributed under the License is distributed on an "AS IS" BASIS,
WITHOUT WARRANTIES OR CONDITIONS OF ANY KIND, either express or implied.
See the License for the specific language governing permissions and
limitations under the License.

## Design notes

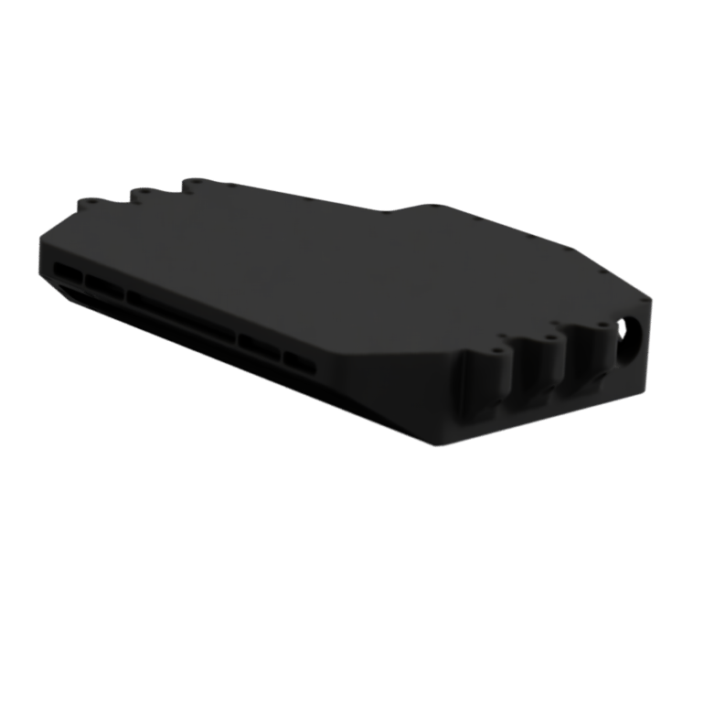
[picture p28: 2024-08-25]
resources/Render/Odyssey Controller Casing (Transparent).png

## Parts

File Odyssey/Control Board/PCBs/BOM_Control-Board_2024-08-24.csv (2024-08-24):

ID | Name | Designator | Footprint | Quantity | Manufacturer Part | Manufacturer | Supplier | Supplier Part | Price | Pins | 3DModel | Contributor | JLCPCB Part Class | link
1 | 0Ω | R4 | R0603 | 1 | 0603WAF0000T5E | UNI-ROYAL(厚声) | LCSC | C21189 | 0.001 | 2 | R0603 | lcsc | Basic Part | https://www.mouser.in/datasheet/2/447/PYu_RT_1_to_0_01_RoHS_L_11-1669912.pdf
2 | 2.2nF | C8 | C0805 | 1 | CL21C222JBFNNNE | SAMSUNG(三星) | LCSC | C28260 | 0.029 | 2 | C0805_L2.0-W1.3-H1.3 | lcsc | Basic Part | https://item.szlcsc.com/373011.html
3 | 10kΩ | R2,R5,R3,R1,R13,R15,R17,R19 | R0603 | 8 | 0603WAF1002T5E | UNI-ROYAL(厚声) | LCSC | C25804 | 0.001 | 2 | R0603 | lcsc | Basic Part | https://www.mouser.in/datasheet/2/447/PYu_RT_1_to_0_01_RoHS_L_11-1669912.pdf
4 | BC807-25_C908258 | Q1 | SOT-23-3_L2.9-W1.3-P1.90-LS2.4-BR | 1 | BC807-25 | FUXINSEMI(富芯森美) | LCSC | C908258 | 0.012 | 3 | SOT-23-3P_L2.9-W1.3-H1.0-LS2.4-P0.95 | LCSC | Extended Part | https://www.diodes.com/assets/Package-Files/SOT23.pdf
5 | 10uF | C6,C15 | C0402 | 2 | CL05A106MQ5NUNC | SAMSUNG(三星) | LCSC | C15525 | 0.004 | 2 | C0402_L1.0-W0.5-H0.5 | lcsc | Basic Part | https://item.szlcsc.com/15869.html
6 | RT9080-33GJ5 | U2 | TSOT-23-5_L2.9-W1.6-P0.95-LS2.8-BL | 1 | RT9080-33GJ5 | RICHTEK(立锜) | LCSC | C841192 | 0.137 | 5 | TSOT-23-5_L2.9-W1.6-H1.00-LS2.8-P0.95 | LCSC | Extended Part | https://item.szlcsc.com/233411.html
7 | 100nF | C2,C5,C1,C9,C13,C14,C3 | C0603 | 7 | CC0603KRX7R9BB104 | YAGEO(国巨) | LCSC | C14663 | 0.002 | 2 | C0603_L1.6-W0.8-H0.8 | lcsc | Basic Part | https://item.szlcsc.com/362304.html
8 | MPU-6050_C24112 | U5 | QFN-24_L4.0-W4.0-P0.50-BL-EP2.7 | 1 | MPU-6050 | TDK InvenSense(应美盛) | LCSC | C24112 | 7.87 | 25 | QFN-24_L4.0-W4.0-P0.50-BL-EP2.7 | lcsc | Extended Part | https://item.szlcsc.com/245167.html
9 | IRLML6244TRPBF | BRTL_F_MOS,BRTL_R_MOS,BRTR_F_MOS,BRTR_R_MOS | SOT-23-3_L2.9-W1.3-P1.90-LS2.4-BR | 4 | IRLML6244TRPBF | Infineon(英飞凌) | LCSC | C143946 | 0.108 | 3 | SOT-23-3P_L2.9-W1.3-H1.0-LS2.4-P0.95 | LCSC | Extended Part | https://www.diodes.com/assets/Package-Files/SOT23.pdf
10 | 22uF | C10 | C0603 | 1 | CL10A226MQ8NRNC | SAMSUNG(三星) | LCSC | C59461 | 0.008 | 2 | C0603_L1.6-W0.8-H0.8 | lcsc | Basic Part | https://item.szlcsc.com/362304.html
11 | XT30PW-M | CN5 | CONN-TH_XT30PW-M | 1 | XT30PW-M | AMASS(艾迈斯) | LCSC | C431092 | 0.358 | 4 | CONN-TH_XT30PW-M | LCSC | Extended Part | https://cn.bing.com/search?q=datasheet: XT30PW-M
12 | BM06B-GHS-TBT(LF)(SN)(N | FINGERPRINT | CONN-SMD_6P-P1.25_BM06B-GHS-TBT-LF-SN-N | 1 | BM06B-GHS-TBT(LF)(SN) | JST | LCSC | C189892 | 0.245 | 8 | CONN-SMD_GH1.25-LS-6P | LCSC | Extended Part | https://lcsc.com/product-detail/Wire-To-Board-Wire-To-Wire-Connector_JST-Sales-America_BM06B-GHS-TBT-LF-SN-N_JST-Sales-America-BM06B-GHS-TBT-LF-SN-N_C189892.h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
13 | PM2.54-1*6 | FLASH | HDR-TH_6P-P2.54-V-F | 1 | PM2.54-1*6 | ZHOURI(洲日) | LCSC | C5224026 | 0.072 | 6 | HDR-TH_6P-P2.54-V-F | lcsc | Extended Part | https://so.szlcsc.com/global.html?c=&k=C40877
14 | SM15B-GHS-TB(LF)(SN) | FRONT,REAR | CONN-SMD_15P-P1.25_SM15B-GHS-TB-LF-SN | 2 | SM15B-GHS-TB(LF)(SN) | JST | LCSC | C265027 | 0.481 | 17 | CONN-SMD_GH1.25-LS-15P | LCSC | Extended Part | https://lcsc.com/product-detail/Wire-To-Board-Wire-To-Wire-Connector_JST-Sales-America_SM15B-GHS-TB-LF-SN_JST-Sales-America-SM15B-GHS-TB-LF-SN_C265027.html
15 | 100Ω | R12,R16,R18,R20 | R0603 | 4 | 0603WAF1000T5E | UNI-ROYAL(厚声) | LCSC | C22775 | 0.001 | 2 | R0603 | lcsc | Basic Part | https://www.mouser.in/datasheet/2/447/PYu_RT_1_to_0_01_RoHS_L_11-1669912.pdf
16 | TLP172GM(TPL,E(O | U3 | SMD-4_L4.6-W3.7-P2.54-LS7.0-BR | 1 | TLP172GM(TPL,E(O | TOSHIBA(东芝) | LCSC | C261926 | 0.527 | 4 | SMD-4_L3.7-W4.6-H2.2-LS7.0-P2.54 | LCSC | Extended Part | https://atta.szlcsc.com/upload/public/pdf/source/20171211/C146278_15129763520271175318.pdf
17 | ESP32-WROOM-32E(8MB) | U9 | WIFI-SMD_ESP32-WROOM-32E | 1 | ESP32-WROOM-32E(8MB) | Espressif Systems | LCSC | C701342 | 4.72 | 47 | WIFI-SMD_L25.5-W18.0-H3.1-ESP32-WROOM-32E | LCSC | Extended Part | https://atta.szlcsc.com/upload/public/pdf/source/20220601/0020821B65DE5740BBACA5FACC5CF3B6.pdf
18 | BM02B-GHS-TBT (LF)(SN) | VESC-ENABLE | CONN-SMD_2P-P1.25_BM02B-GHS-TBT-LF-SN | 1 | BM02B-GHS-TBT(LF)(SN) | JST | LCSC | C161690 | 0.108 | 4 | CONN-SMD_GH1.25-LS-2P | LCSC | Extended Part | https://lcsc.com/product-detail/Wire-To-Board-Wire-To-Wire-Connector_JST-Sales-America_BM02B-GHS-TBT-LF-SN_JST-Sales-America-BM02B-GHS-TBT-LF-SN_C161690.html
19 | SN74AHCT125DR | U4 | SOIC-14_L8.7-W3.9-P1.27-LS6.0-BL | 1 | SN74AHCT125DR | TI(德州仪器) | LCSC | C155176 | 0.182 | 14 | SOIC-14_L8.6-W3.9-H1.8-LS6.0-P1.27 | LCSC | Extended Part | https://item.szlcsc.com/7253.html
20 | JFC2410-1400TS | F1 | FUSE-SMD_L6.1-W2.6 | 1 | JFC2410-1400TS | JDTfuse(集电通) | LCSC | C136386 | 0.069 | 2 | FUSE-SMD_L6.1-W2.6-H2.6 | LCSC | Extended Part | https://item.szlcsc.com/349666.html

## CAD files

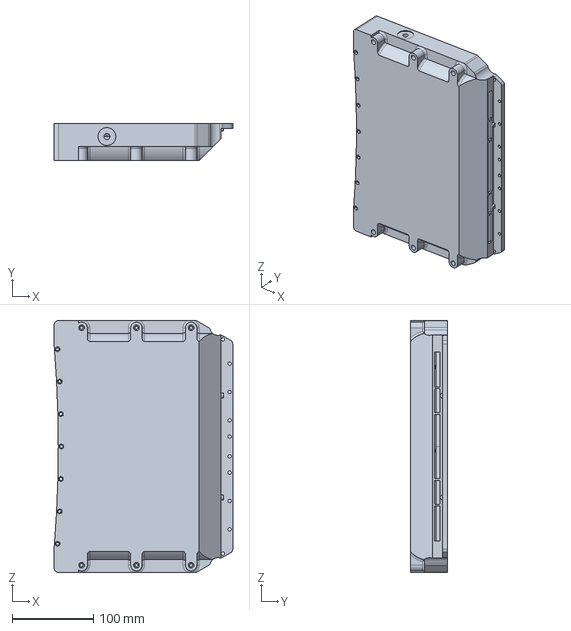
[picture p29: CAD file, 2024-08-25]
Odyssey/Battery Casing/Odyssey Battery Casing.step
220.2 x 45.5 x 310.8 mm

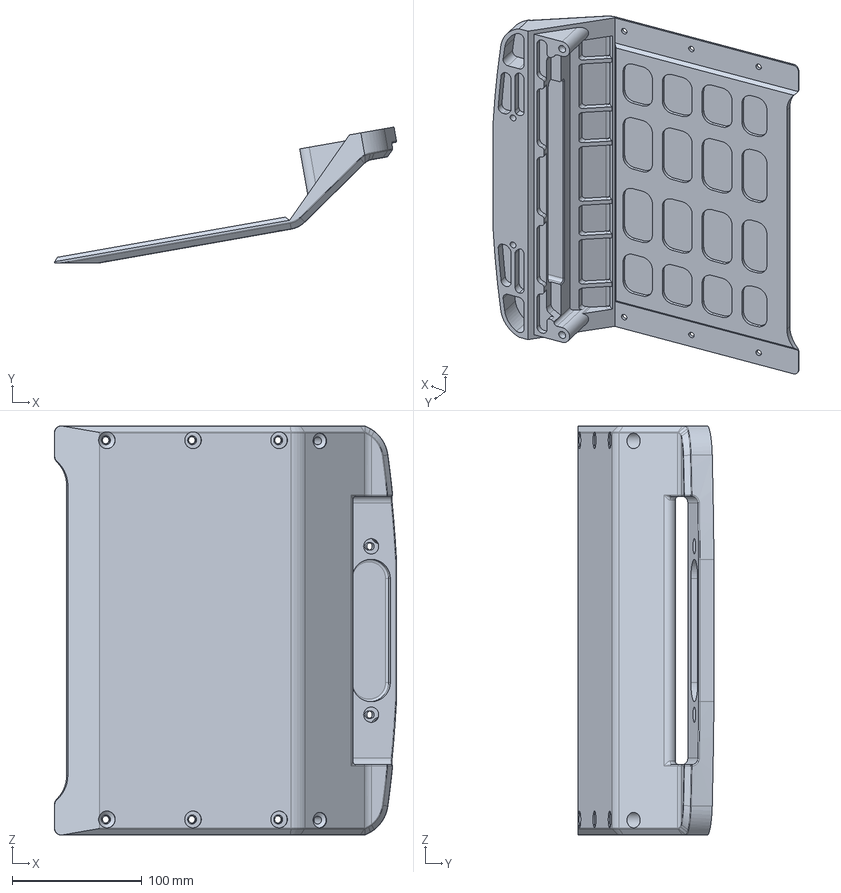
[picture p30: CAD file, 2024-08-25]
Odyssey/Bumpers/Odyssey Bumper.step
264.1 x 105.0 x 315.8 mm

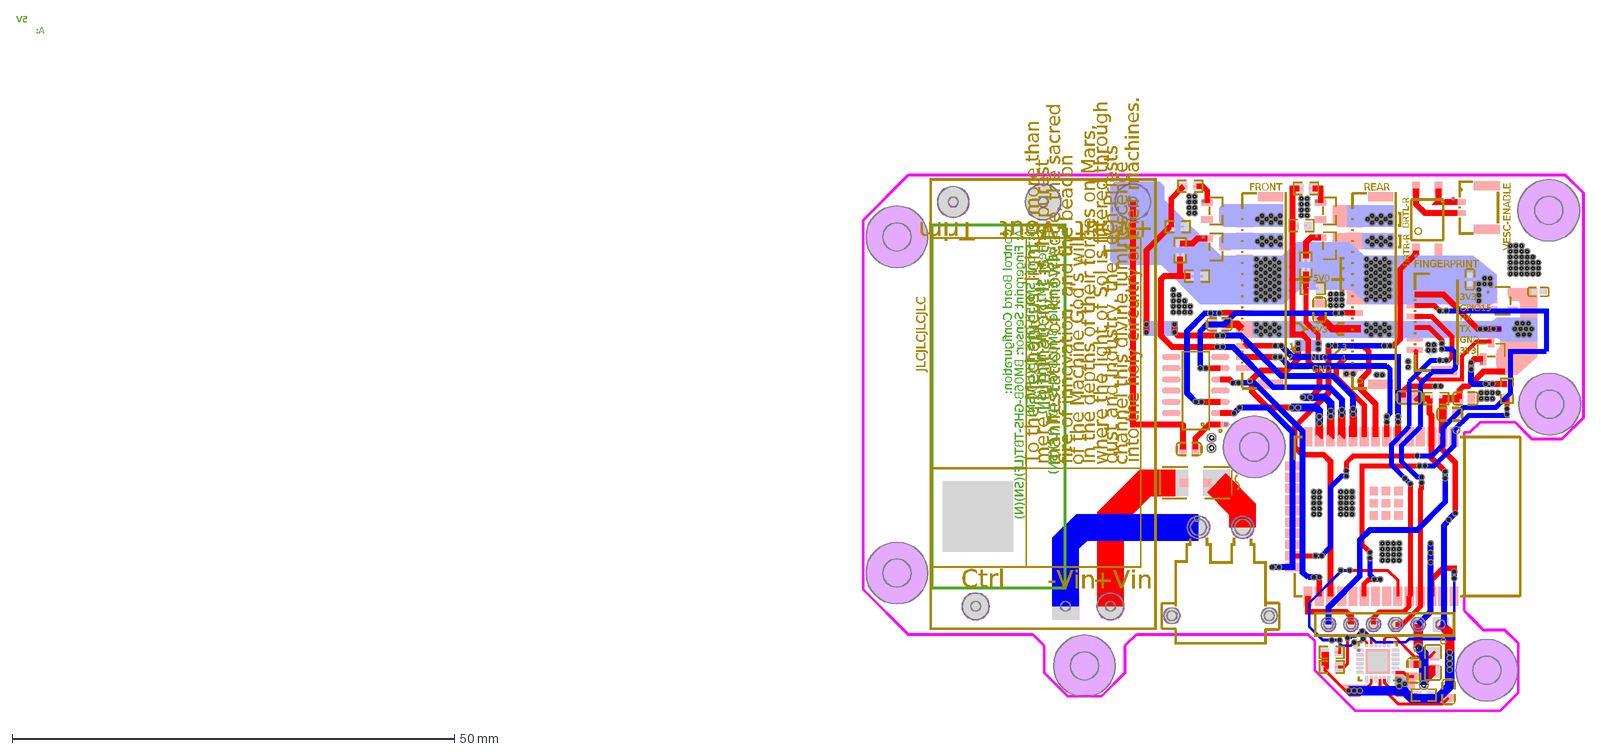
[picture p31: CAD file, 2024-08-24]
Odyssey/Control Board/PCBs/Drawing (DXF)/PCB_Control-Board_2024-08-24.dxf
3V3
GND
BRTR-R
BRTL-R
JLCJLCJLCJLC
To the Mechanicus, light is more than
mere illumination; it is the purest
manifestation of knowledge, the sacred
fire of innovation, and the beacon
In the depths of their forges on Mars,
where the light of Sol is filtered through
of the Machine God's will.
dust and industry, the Tech-Priests
channel this divine luminescence
into the holy circuitry of their machines.
2
NTC
TX
RX
GPIO15
1
3
4
5V0
5V
A:
D: VESC-Enable: BM02B-GHS-TBT (LF)(SN)
C: Rear: SM15B-GHS-TB(LF)(SN)
B: Front: SM15B-GHS-TB(LF)(SN)
A: Fingerprint Sensor: BM06B-GHS-TBT(LF)(SN)(N)
Control Board Configuration:
FINGERPRINT
FRONT
REAR
-Vin
+Vin
Ctrl
+Vout
-Vout
Trim
VESC-ENABLE

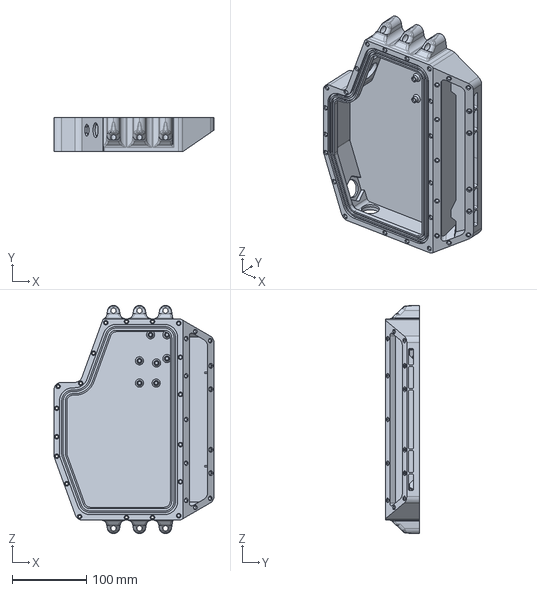
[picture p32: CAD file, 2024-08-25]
Odyssey/Controller Casing/Odyssey Controller Casing.step
215.2 x 45.5 x 306.8 mm

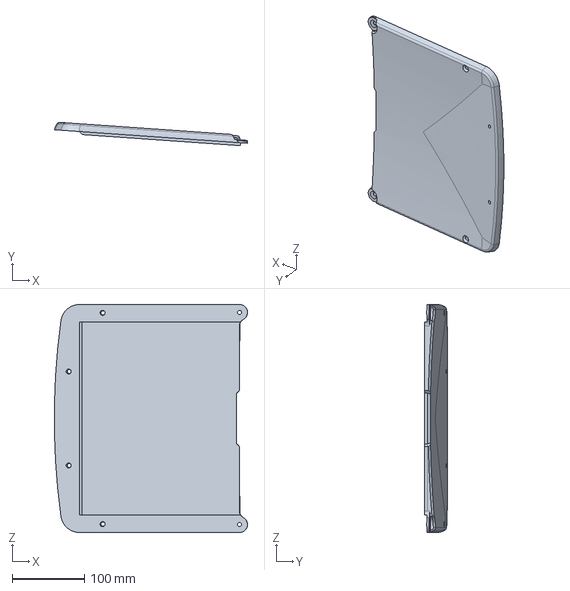
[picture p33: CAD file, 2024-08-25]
Odyssey/Footpads/Footpad (Odyssey)(Concave).step
267.6 x 32.3 x 315.8 mm

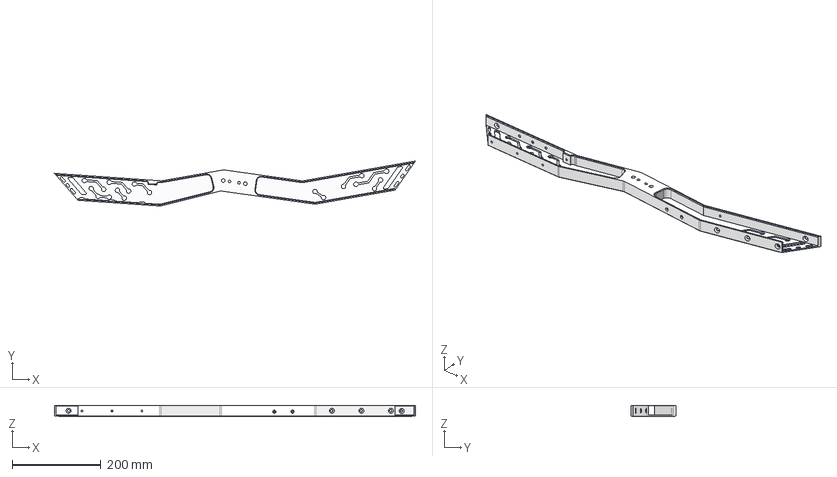
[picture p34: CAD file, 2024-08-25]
Odyssey/Rails/Odyssey Rails (Skeletonised)/Odyssey Rail (R) (Skeletonised).step
813.9 x 101.5 x 25.0 mm

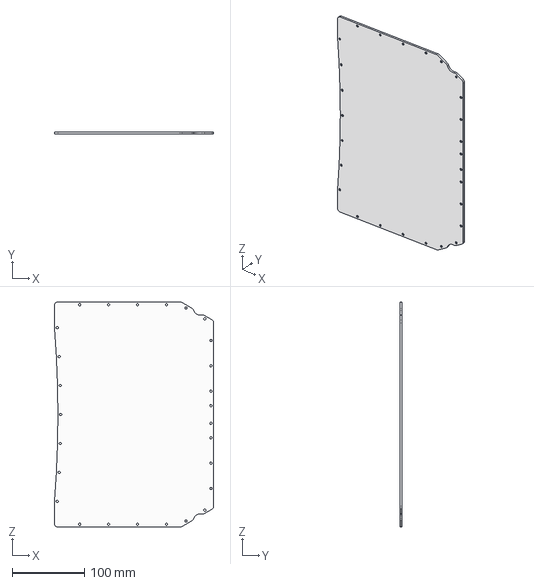
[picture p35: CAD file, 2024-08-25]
Odyssey/Battery Casing/Odyssey Battery Casing (Lid).step
220.2 x 3.00 x 310.8 mm

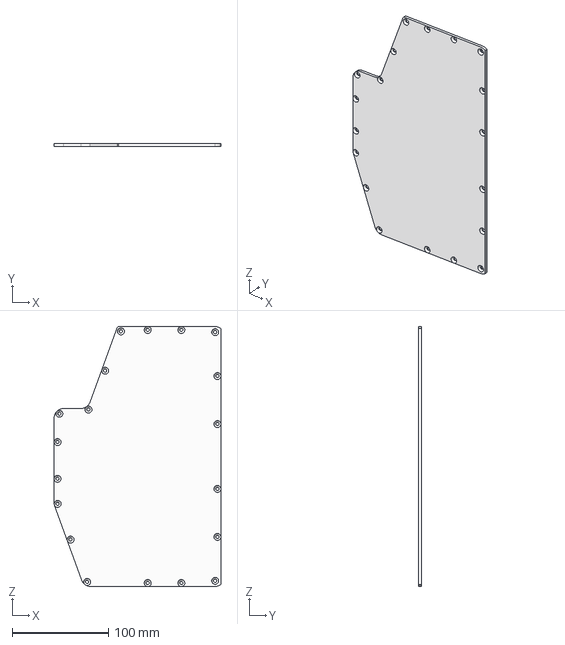
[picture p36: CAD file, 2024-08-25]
Odyssey/Controller Casing/Odyssey Controller Casing (Lid 1).step
173.7 x 3.00 x 270.8 mm

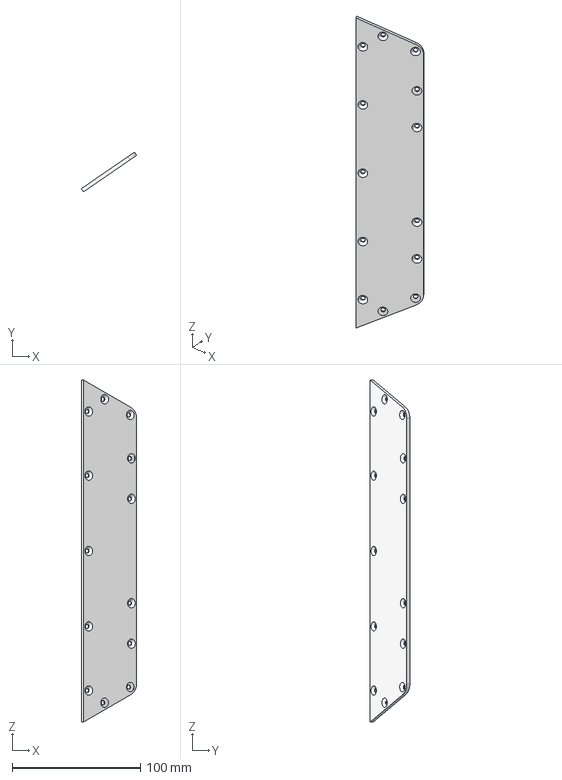
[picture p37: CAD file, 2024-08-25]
Odyssey/Controller Casing/Odyssey Controller Casing (Lid 2).step
43.2 x 31.0 x 266.7 mm

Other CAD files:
Odyssey/LightSym Bar/PCBs/Drawing (DXF)/PCB_Lightbar-Sym_2024-08-25.dxf
Odyssey/Rails/Odyssey Rails/Odyssey Rail (L) (Skeletonised).step
Odyssey/Rails/Odyssey Rails (Skeletonised)/Odyssey Rail (L) (Skeletonised).step
Odyssey/Bumpers/Odyssey Bumper.f3d
Odyssey/Footpads/Footpad (Odyssey)(Concave).f3d
Odyssey/Rails/Odyssey Rails (Skeletonised)/Odyssey Rail (L) (Skeletonised).f3d
Odyssey/Rails/Odyssey Rails (Skeletonised)/Odyssey Rail (R) (Skeletonised).f3d
Odyssey/Rails/Odyssey Rails/Odyssey Rail (L) (Skeletonised).f3d
Odyssey/Rails/Odyssey Rails/Odyssey Rail (R) (Skeletonised).f3d

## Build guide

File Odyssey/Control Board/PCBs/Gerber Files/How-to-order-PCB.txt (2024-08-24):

How to Order PCB

Please refer to:
https://docs.easyeda.com/en/PCB/Order-PCB

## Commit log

2024-08-24 Initial V1.0.0 File Upload
    V1.0.0 is the initial version of the Avalon Series Boards. This version is untested and only for internal testing only.
    [Avalon-Series-Control-Board_2024-08-24.schdoc, BOM_Control-Board_2024-08-24.csv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]
2024-08-25 V1.0.0 Intial Version
    Second Resource dump of initial commit. Includes STEP Files and More PCB Gerber/EasyEDA files
    [Avalon-Series-Control-Board_2024-08-24.schdoc, BOM_Control-Board_2024-08-24.csv, Footpad (Odyssey)(Concave).f3d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]
2024-08-25 V1.0.0 File organisation
    Moved the rails files around to allow for the non-skeletonised versions to be added
    [Odyssey Rail (L) (Skeletonised).f3d, Odyssey Rail (L) (Skeletonised).step, Odyssey Rail (R) (Skeletonised).f3d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]
2024-08-26 Update README.md
    Reformatted readme.md and added calculations for current consumption across Odyssey Control Board.
